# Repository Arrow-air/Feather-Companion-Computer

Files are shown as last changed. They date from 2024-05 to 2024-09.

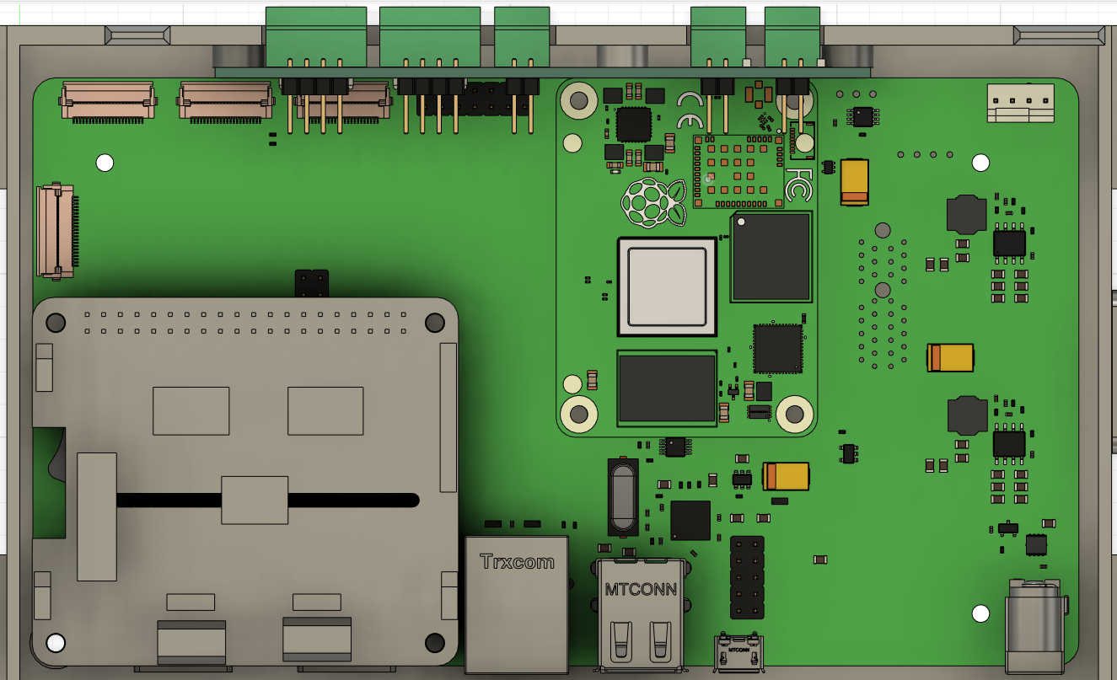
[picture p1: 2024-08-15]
Docs/FCPC Exposed Pic.png

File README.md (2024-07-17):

# Feather Flight Companion Computer

## Ground Control Station & Onboard Flight UI

### Functions:
1. Data Logger
2. Telemetry Server
3. User Interface Engine

## Table of Contents
1. [Introduction](#introduction)
2. [Architecture Overview](#architecture-overview)
3. [File Descriptions](#file-descriptions)
    - [FCPC.py](#fcpcpy)
    - [Data.py](#datapy)
    - [Veronte.py](#verontepy)
    - [BMS.py](#bmspy)
    - [VESCCAN.py](#vesccanpy)
    - [ESC.py](#escpy)
    - [CyphalCAN3.py](#cyphalcan3py)
    - [TCP.py](#tcppy)
    - [server.py](#serverpy)
    - [protocols_functions.py](#protocols_functionspy)
    - [display1.py](#display1py)
    - [display2.py](#display2py)
    - [Joystick.py](#joystickpy)
    - [LoRa.py](#lorapy)
    - [IO.py](#iopy)

## Introduction

The Flight Companion Computer system designed for both Ground Control Station (GCS) and onboard flight use (FUI). It integrates multiple functionalities including data logging, telemetry server, and a user interface engine. The system is modular, allowing for easy expansion and maintenance, and is designed to provide a robust Data interface for flight operations.

## Architecture Overview

The system is structured into multiple modules, each handling a specific aspect of the overall functionality. These modules include communication protocols, data handling, user interfaces, and specific hardware controls. The main control program loop resides in the `FCPC.py` file.

## File Descriptions

### FCPC.py
**Main Function and Control Logic**  
The central script that coordinates the activities of all other modules. Handles high-level decision making and ensures smooth operation of the entire system.

### Data.py
**Data Handling Module**  
Manages data storage and retrieval within the system. Provides functions for logging data, managing data formats, packaging data to be sent as telemetry.

### Veronte.py
**Veronte Module**  
Interfaces with the main Flight Controller, the Embention Veronte X1, over UART serial. packages flight sensor data, such as attitude and altitude etc.

### BMS.py
**Battery Management System (BMS) Module**  
Packages data from each of the 6 Ennoid X-LITE-V4 BMSs on board the aircraft, including voltage, current, temperature, and state of charge, etc.

### VESCCAN.py
**VESC-CAN Module**  
Interfaces with the VESC CAN bus protocol for interacting with data emminating from the Ennoid X-LITE-V4 BMSs, as implemented by Ennoid.

### ESC.py
**Electronic Speed Controller (ESC) Module**  
Packages data from each of the 6 Mad Motors ECSs on board the aircraft, including voltage, current, temperature, and state of charge, etc.

### CyphalCAN3.py
**Cyphal-CAN Protocol Module**  
Interfaces with the Cyphal-CAN CAN bus protocol for interacting with data emminating from the MAD Motors ECS, as implemented by MAD Motors.

### TCP.py
**TCP/IP Communication Module**  
Implements communication over TCP/IP, handling socket connections, data transmission, and reception over local network, send telemetry data to the displays.

### server.py
**Server Module**  
Sets up a network connection to `display1.py` and `display2.py` to send telementry data to the display screens

### protocols_functions.py
**Protocols Utility Functions Module**  
Contains utility functions used by `server.py`, `display1.py`, and `display2.py`. Provides common functionalities such as message parsing, checksum calculation, and other specific operations.

### display1.py
**Display Module 1**  
Responsible for rendering the "System State Window", primarily displaying data from the Flight Controller.

### display2.py
**Display Module 2**  
Responsible for rendering the "System Infromation Window", primarily displaying data from all the ESCs and BMSs.

### Joystick.py
**Joystick Input Module**  
Handles input from but Logitec USB and Otto CAN joystick devices. Reads joystick movements and button presses, translating their commands to the control system.

### LoRa.py
**Long Range Radio Communication Module**  
Implements communication over the LoRa protocol for long-range, low-power wireless communication. Handles message encoding, decoding, and transmission.

### IO.py
**Input-Output Module**  
Manages I/O on the RPI GPIO pins.

---

This README provides a comprehensive overview of the Project Feather system and its components. For detailed usage and additional information, refer to the documentation within each module and the main `FCPC.py` script, as well as the following reference documents:

## FCPC Concept Document 

[FCPC Concept]( https://docs.google.com/document/d/15r7cTYvV1hOLt8er7vyQtWU0twEOfAIIOQ0pdE-wRtA/edit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 )

## Project Feather Data Network & Ground Equipment Document

[Data Network & Ground Equipment]( https://docs.google.com/document/d/11VlSYsE245VFLZsYB7TvqWuuJ1UnPRjPKnnLWUzqcEM/edit )

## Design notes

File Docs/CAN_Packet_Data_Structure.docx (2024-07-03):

# CAN Packet Data Structure

CAN Packet | Frame ID | Extended Frame | Length | Signal | Start Bit | Length | Byte Order | Signed | Scale | Offset | Minimum | Maximum | Unit
CAN_PACKET_BMS_TEMPS | 11018 | Yes | 8 | NoOfCells | 15 | 8 | Big Endian | No | 1 | 0 | 0 | 1
| | | | auxVoltagesIndividual1 | 23 | 16 | Big Endian | No | 0.01 | 0
| | | | auxVoltagesIndividual2 | 39 | 16 | Big Endian | No | 0.01 | 0
| | | | auxVoltagesIndividual3 | 55 | 16 | Big Endian | No | 0.01 | 0
CAN_PACKET_BMS_V_TOT | 9738 | Yes | 8 | packVoltage | 7 | 32 | Big Endian | Yes | 1 | 0 | -3.4e+38 | 3.4e+38 | V
| | | | chargerVoltage | 39 | 32 | Big Endian | Yes | 1 | 0 | 0 | 1 | V
CAN_PACKET_BMS_I | 9994 | Yes | 8 | packCurrent1 | 7 | 32 | Big Endian | Yes | 1 | 0 | 0 | 1 | A
| | | | packCurrent2 | 39 | 32 | Big Endian | Yes | 1 | 0 | 0 | 1 | A
CAN_PACKET_BMS_AH_WH | 10250 | Yes | 8 | Ah_Counter | 7 | 32 | Big Endian | Yes | 1 | 0 | 0 | 1 | Ah
| | | | Wh_Counter | 39 | 32 | Big Endian | Yes | 1 | 0 | 0 | 1 | Wh
CAN_PACKET_BMS_V_CELL | 10506 | Yes | 8 | cellPoint | 7 | 8 | Big Endian | No | 1 | 0 | 0 | 48
| | | | NoOfCells | 15 | 8 | Big Endian | No | 1 | 0 | 0 | 48
| | | | cellVoltage10 | 23 | 16 | Big Endian | No | 0.001 | 0 | 0 | 1 | V
| | | | cellVoltage11 | 39 | 16 | Big Endian | No | 0.001 | 0 | 0 | 1 | V
| | | | cellVoltage12 | 55 | 16 | Big Endian | No | 0.001 | 0 | 0 | 1 | V
CAN_PACKET_BMS_BAL | 10762 | Yes | 8 | NoOfCells | 0 | 8 | Little Endian | Yes | 1 | 0
| | | | bal_state | 8 | 56 | Little Endian | Yes | 1 | 0 | 0 | 1
CAN_PACKET_BMS_SOC_SOH_TEMP_STAT | 11530 | Yes | 8 | cellVoltageLow | 7 | 16 | Big Endian | No | 0.001 | 0 | 0 | 1 | V
| | | | cellVoltageHigh | 23 | 16 | Big Endian | No | 0.001 | 0 | 0 | 1 | V
| | | | SOC | 39 | 8 | Big Endian | No | 0.392156863 | 0 | 0 | 1 | %
| | | | SOH | 47 | 8 | Big Endian | No | 0.3922 | 0 | 0 | 100 | %
| | | | tBattHi | 55 | 8 | Big Endian | No | 1 | 0 | 0 | 1 | C
| | | | BitF | 63 | 8 | Big Endian | No | 1 | 0 | 0 | 1
CAN_PACKET_BMS_HUM | 11274 | Yes | 6 | CAN_PACKET_BMS_TEMP0 | 7 | 16 | Big Endian | No | 0.01 | 0 | 0 | 1 | C
| | | | CAN_PACKET_BMS_HUM_HUM | 23 | 16 | Big Endian | No | 0.01 | 0 | 0 | 1 | %
| | | | CAN_PACKET_BMS_HUM_TEMP1 | 39 | 16 | Big Endian | No | 0.01 | 0 | 0 | 1 | C

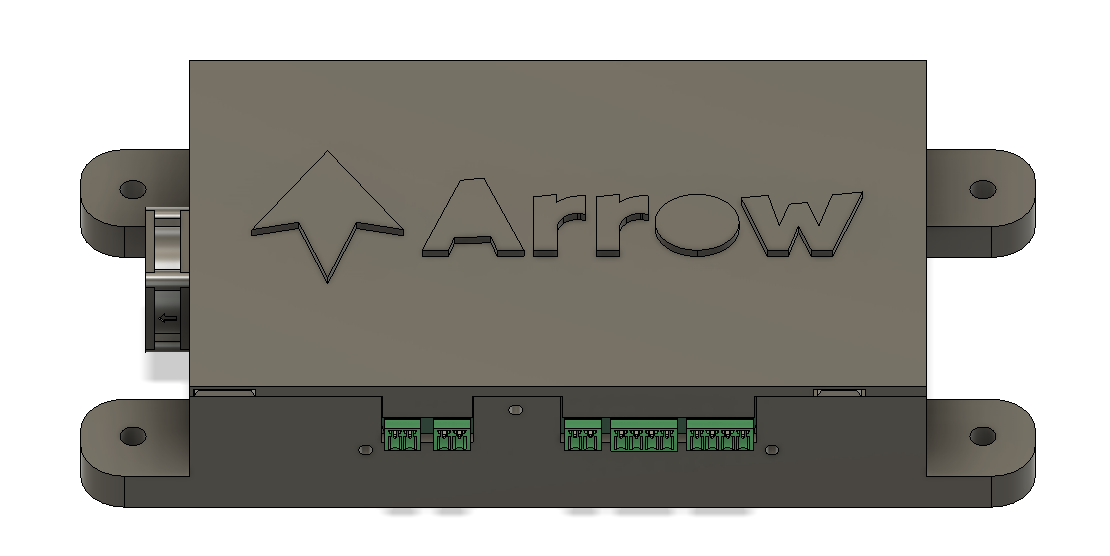
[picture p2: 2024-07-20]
Hardware/Enclosure/Front.png

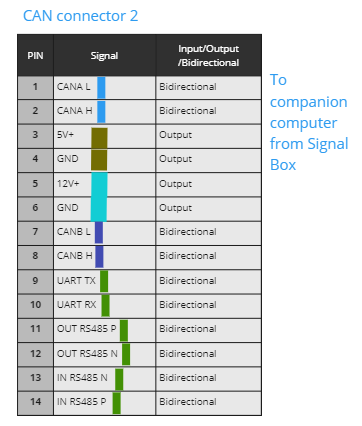
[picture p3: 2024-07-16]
Hardware/PCBs/FCPC Breakout PCB/Connectors to FCPC.PNG

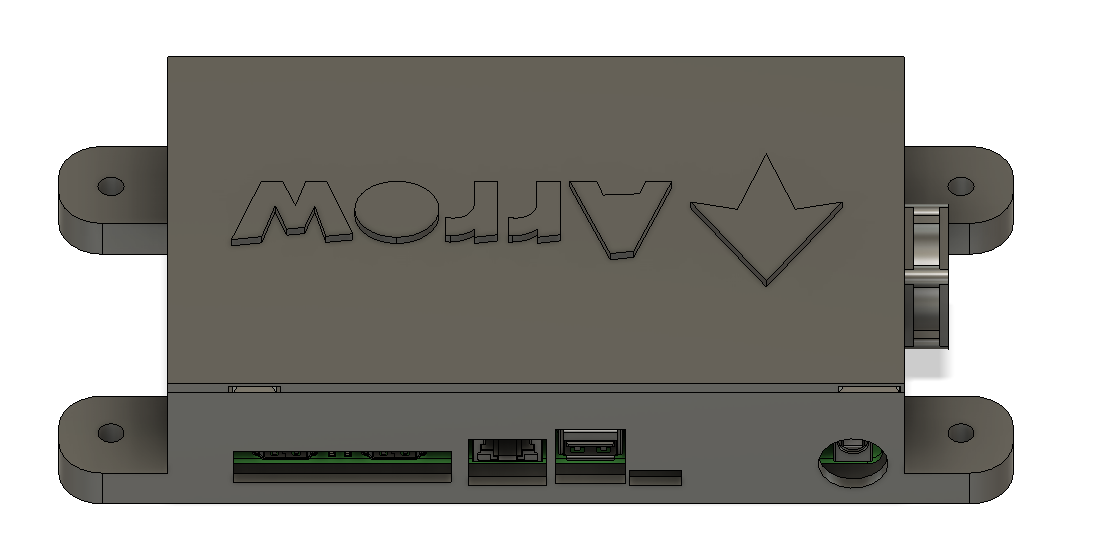
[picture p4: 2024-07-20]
Hardware/Enclosure/Back.png

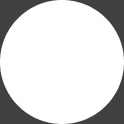
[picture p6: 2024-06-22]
images/inner circle.png

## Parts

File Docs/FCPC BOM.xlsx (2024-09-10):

Name | Description | Link | Price | Qty | Shipping + Tax | Total | Status | Notes
Companion PC | Raspberry Pi CM4 (NO WIFI NO Bluetooth) + IO Board (One on Craft Another on Ground) | https://www.digikey.co.uk/en/products/detail/raspberry-pi/SC0687/13530926 | $80.00 | 2 |  | $160.00 |  | Estimated
Displays | Groud station replica | https://www.elecrow.com/elecrow-10-1-inch-display-ips-1280x800-acrylic-case-touch-screen-compatible.html | $80.00 | 4 |  | $320.00 |  | Estimated
Control Sticks | Otto sticks, (or potential alternative (e.g Megatron)) | https://www.otto-controls.com/products/joysticks/Joystick%20Bases%20and%20Grips/HJLG3-M%20Joystick%20with%20Grip | $400.00 | 3 |  | $1,200.00 |  | Estimated
Enclosures + Mounting | Display mounts, 3D printed enclosures, etc | https://github.com/Arrow-air/Feather-Companion-Computer/tree/main/Hardware/Enclosure | $200.00 | 2 |  | $400.00 |  | Estimated
Cooling Fan |  | https://www.amazon.com/Dedicated-Cooling-Designed-Raspberry-Adjustment/dp/B09328RJK2 , https://www.waveshare.com/fan-4010-pwm-12v.htm | $7.90 | 2 |  | $15.8
Breakout PCB | Inhouse Design, wiring breakout Board | https://github.com/Arrow-air/Feather-Companion-Computer/tree/main/Hardware/PCBs/FCPC%20Breakout%20PCB | $25.00 | 2 |  | $50 |  | Estimated
CAN Module | 2 Channel RPi CAN Hat | https://www.waveshare.com/2-ch-can-hat.htm | $21.00 | 1 |  | $21.00
LoRa Modules | Telemetry Over LoRa Comms (HF Version, TCXO) | https://www.waveshare.com/usb-to-lora.htm | $17.99 | 2 |  | $35.98
LoRa Antenna | Range Extension and Location Flexibility (868MHZ version) | https://www.waveshare.com/868-915m-magnet-mount-antenna.htm?sku=24412 | $2.99 | 2 |  | $5.98
Powered USB Hub | 12V Power In over Barrel Jack Connector | e.g https://amzn.eu/d/gOa1naj | $20.00 | 2 |  | $40.00 |  | Estimated
FPV Camera & Transmitter |  | https://amzn.eu/d/8iTdUrI | $230.00 | 1 |  | $230.00 |  | Estimated
FPV Monitor |  | https://amzn.eu/d/cirWO3p | $120.00 | 1 |  | $120.00 |  | Estimated
Long Range WLAN Bridge | Point to Point Wireless Bridge | https://a.co/d/ivutc1m ( potential alternative e.g https://amzn.eu/d/02wFvdkK ) | $90.00 | 1 |  | $90.00 |  | Estimated

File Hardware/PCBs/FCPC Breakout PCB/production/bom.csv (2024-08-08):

Designator | Footprint | Quantity | Value | LCSC Part #
C1, C2 | 0805 | 2 | C
J1 | PhoenixContact_MCV_1,5_4-G-3.5_1x04_P3.50mm_Vertical | 1 | CAN
J10 | PinHeader_1x04_P2.54mm_Vertical | 1 | RS485
J2 | PhoenixContact_MCV_1,5_4-G-3.5_1x04_P3.50mm_Vertical | 1 | RS485
J3 | PhoenixContact_MCV_1,5_2-G-3.5_1x02_P3.50mm_Vertical | 1 | UART
J4 | PhoenixContact_MCV_1,5_2-G-3.5_1x02_P3.50mm_Vertical | 1 | 5V
J5 | PhoenixContact_MCV_1,5_2-G-3.5_1x02_P3.50mm_Vertical | 1 | 12V
J6 | PinHeader_1x02_P2.54mm_Vertical | 1 | UART
J7 | PinHeader_1x04_P2.54mm_Vertical | 1 | CAN
J8 | PinHeader_1x02_P2.54mm_Vertical | 1 | 5V
J9 | PinHeader_1x02_P2.54mm_Vertical | 1 | 12V
R1 | 0805 | 1 | 470
R2 | 0805 | 1 | 1K

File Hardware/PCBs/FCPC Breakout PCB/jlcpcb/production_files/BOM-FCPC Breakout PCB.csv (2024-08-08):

Comment | Designator | Footprint | LCSC
CAN | J1,J2 | PhoenixContact_MCV_1,5_4-G-3.5_1x04_P3.50mm_Vertical | C3580225
UART | J3,J4,J5 | PhoenixContact_MCV_1,5_2-G-3.5_1x02_P3.50mm_Vertical | C3582478
RS485 | J10 | PinHeader_1x04_P2.54mm_Vertical
12V | J9 | PinHeader_1x02_P2.54mm_Vertical
5V | J8 | PinHeader_1x02_P2.54mm_Vertical
CAN | J7 | PinHeader_1x04_P2.54mm_Vertical
UART | J6 | PinHeader_1x02_P2.54mm_Vertical
C | C2 | C_0805_2012Metric_Pad1.18x1.45mm_HandSolder
C | C1 | C_0805_2012Metric_Pad1.18x1.45mm_HandSolder
470 | R1 | R_0805_2012Metric_Pad1.20x1.40mm_HandSolder
1K | R2 | R_0805_2012Metric_Pad1.20x1.40mm_HandSolder

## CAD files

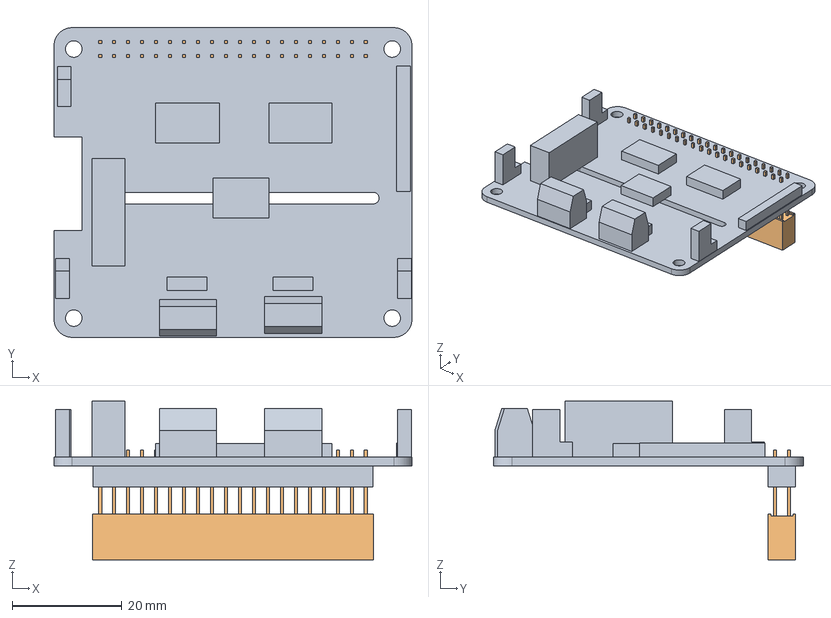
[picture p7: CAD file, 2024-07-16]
Hardware/PCBs/2-CH CAN HAT drawing/j25-2_asm.stp
65.2 x 56.4 x 28.9 mm
J25-2
J25-3

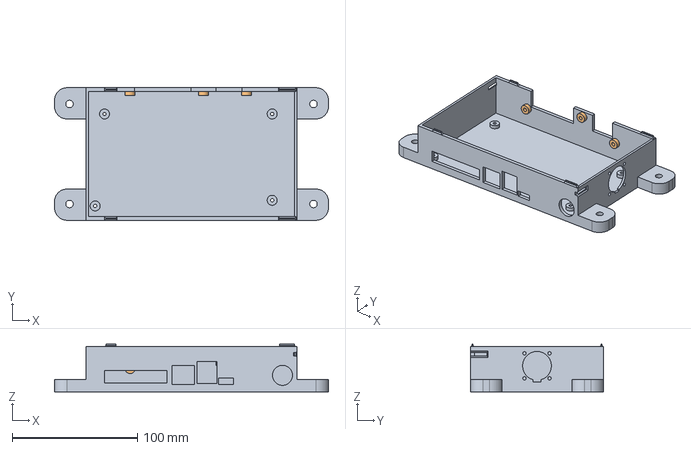
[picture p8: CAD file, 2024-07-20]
Hardware/Enclosure/Base.step
219.0 x 106.0 x 38.0 mm

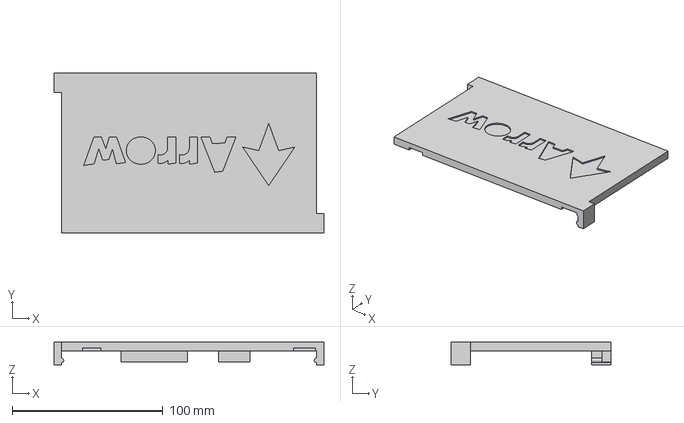
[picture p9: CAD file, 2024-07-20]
Hardware/Enclosure/Top.step
179.0 x 106.0 x 15.0 mm

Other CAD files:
Hardware/Enclosure/Top.stl

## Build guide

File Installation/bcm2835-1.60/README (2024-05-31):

This is a C library for Raspberry Pi (RPi). It provides access to 
GPIO and other IO functions on the Broadcom BCM 2835 chip.
allowing access to the 
26 pin ISE plug on the RPi board so you can control and interface with various
external devices.

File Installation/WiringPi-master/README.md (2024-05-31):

WiringPi (Unofficial Mirror/Fork)
=================================

This is an unofficial mirror/fork of wiringPi to support ports (Python/Ruby/etc).  With the
[end of official development](https://web.archive.org/web/20220405225008/http://wiringpi.com/wiringpi-deprecated/), this repository
has become a mirror of the last "official" source release, plus a fork facilitating updates
to support newer hardware (primarily for use by the ports) and fix bugs.

  * The final "official" source release can be found at the
    [`final_source_2.50`](https://github.com/WiringPi/WiringPi/tree/final_official_2.50) tag.
  * The default `master` branch contains code that has been written since that final source
    release to provide support for newer hardware.

Ports
-----

wiringPi has been wrapped for multiple languages:

* Node - https://github.com/WiringPi/WiringPi-Node
* Perl - https://github.com/WiringPi/WiringPi-Perl
* PHP - https://github.com/WiringPi/WiringPi-PHP
* Python - https://github.com/WiringPi/WiringPi-Python
* Ruby - https://github.com/WiringPi/WiringPi-Ruby

Support
-------

Please do not email Gordon if you have issues, he will not be able to help.

Pull-requests may be accepted to add or fix support for newer hardware, but new features or
other changes may not be accepted.

For support, comments, questions, etc please join the WiringPi Discord channel: https://discord.gg/SM4WUVG

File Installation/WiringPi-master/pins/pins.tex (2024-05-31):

\documentclass[12pt,a4paper]{article}
\parskip 1ex
\parindent 0em
\thispagestyle{empty}
\pagestyle{plain}
\pagenumbering{arabic}
\setlength{\topmargin}{0pt}
\setlength{\headheight}{0pt}
\setlength{\headsep}{0pt}
\setlength{\topskip}{0pt}
\setlength{\textheight}{240mm}
\setlength{\footskip}{5ex}
\setlength{\oddsidemargin}{0pt}
\setlength{\evensidemargin}{0pt}
\setlength{\textwidth}{160mm}
\usepackage[dvips]{graphics,color}
\usepackage{helvet}
\renewcommand{\familydefault}{\sfdefault}
\begin{document}
\begin{sffamily}
\definecolor{rtb-black}{rgb}  {0.0, 0.0, 0.0}
\definecolor{rtb-navy}{rgb}   {0.0, 0.0, 0.5}
\definecolor{rtb-green}{rgb}  {0.0, 0.5, 0.0}
\definecolor{rtb-teal}{rgb}   {0.0, 0.5, 0.5}
\definecolor{rtb-maroon}{rgb} {0.5, 0.0, 0.0}
\definecolor{rtb-purple}{rgb} {0.5, 0.0, 0.5}
\definecolor{rtb-olive}{rgb}  {0.5, 0.5, 0.0}
\definecolor{rtb-silver}{rgb} {0.7, 0.7, 0.7}
\definecolor{rtb-grey}{rgb}   {0.5, 0.5, 0.5}
\definecolor{rtb-blue}{rgb}   {0.0, 0.0, 1.0}
\definecolor{rtb-lime}{rgb}   {0.0, 1.0, 0.0}
\definecolor{rtb-aqua}{rgb}   {0.0, 1.0, 1.0}
\definecolor{rtb-red}{rgb}    {1.0, 0.0, 0.0}
\definecolor{rtb-fuchsia}{rgb}{1.0, 0.0, 1.0}
\definecolor{rtb-yellow}{rgb} {1.0, 1.0, 0.0}
\definecolor{rtb-white}{rgb}  {1.0, 1.0, 1.0}

\begin{center}
\bfseries{WiringPi: GPIO Pin Numbering Tables}\\
\tt{https://github.com/WiringPi/WiringPi}
\end{center}

\begin{center}
\begin{tabular}{|c|c|c||p{8mm}|p{8mm}||c|c|c|c|}
\hline
\multicolumn{8}{|c|}{\bfseries{P1: The Main GPIO connector}}\\
\hline
\hline
WiringPi Pin	& BCM GPIO	& Name	& \multicolumn{2}{|c||}{Header}	& Name	& BCM GPIO	& WiringPi Pin\\
\hline
\hline
	& 			& \textcolor{rtb-red}{3.3v}	& \raggedleft{1} &  2 & \textcolor{rtb-maroon}{5v}	& 	& \\
\hline
8	& Rv1:0 - Rv2:2		& \textcolor{rtb-aqua}{SDA}	& \raggedleft{3} &  4 & \textcolor{rtb-maroon}{5v}	& 	& \\
\hline
9	& Rv1:1 - Rv2:3		& \textcolor{rtb-aqua}{SCL}	& \raggedleft{5} &  6 & \textcolor{rtb-black}{0v}	& 	& \\
\hline
7	& 4			& \textcolor{rtb-green}{GPIO7}	& \raggedleft{7} &  8 & \textcolor{rtb-yellow}{TxD}	& 14    & 15\\
\hline
	& 			& \textcolor{rtb-black}{0v}	& \raggedleft{9} & 10 & \textcolor{rtb-yellow}{RxD}	& 15	& 16\\
\hline
0	& 17			& \textcolor{rtb-green}{GPIO0}	& \raggedleft{11} & 12 & \textcolor{rtb-green}{GPIO1}	& 18	& 1\\
\hline
2	& Rv1:21 - Rv2:27	& \textcolor{rtb-green}{GPIO2}	& \raggedleft{13} & 14 & \textcolor{rtb-black}{0v}	& 	& \\
\hline
3	& 22			& \textcolor{rtb-green}{GPIO3}	& \raggedleft{15} & 16 & \textcolor{rtb-green}{GPIO4}	& 23	& 4\\
\hline
	& 			& \textcolor{rtb-red}{3.3v}	& \raggedleft{17} & 18 & \textcolor{rtb-green}{GPIO5}	& 24	& 5\\
\hline
12	& 10			& \textcolor{rtb-teal}{MOSI}	& \raggedleft{19} & 20 & \textcolor{rtb-black}{0v}	& 	& \\
\hline
13	& 9			& \textcolor{rtb-teal}{MISO}	& \raggedleft{21} & 22 & \textcolor{rtb-green}{GPIO6}	& 25	& 6\\
\hline
14	& 11			& \textcolor{rtb-teal}{SCLK}	& \raggedleft{23} & 24 & \textcolor{rtb-teal}{CE0}	& 8	& 10\\
\hline
	& 			& \textcolor{rtb-black}{0v}	& \raggedleft{25} & 26 & \textcolor{rtb-teal}{CE1}	& 7	& 11\\
\hline
\hline
WiringPi Pin	& BCM GPIO	& Name	& \multicolumn{2}{|c||}{Header}	& Name	& BCM GPIO	& WiringPi Pin\\
\hline
\end{tabular}
\end{center}

Note the differences between Revision 1 and Revision 2 Raspberry
Pi's. The Revision 2 is readily identifiable by the presence of the 2
mounting holes.

The revision 2 Raspberry Pi has an additional GPIO connector, P5, which is next to the main P1 GPIO
connector:

\begin{center}
\begin{tabular}{|c|c|c||p{8mm}|p{8mm}||c|c|c|c|}
\hline
\multicolumn{8}{|c|}{\bfseries{P5: Secondary GPIO connector (Rev. 2 Pi only)}}\\
\hline
\hline
WiringPi Pin	& BCM GPIO	& Name	& \multicolumn{2}{|c||}{Header}	& Name	& BCM GPIO	& WiringPi Pin\\
\hline
\hline
	& 		& \textcolor{rtb-maroon}{5v}	& \raggedleft{1} &  2 & \textcolor{rtb-red}{3.3v}	& 	&	\\
\hline
17	& 28		& \textcolor{rtb-green}{GPIO8}	& \raggedleft{3} &  4 & \textcolor{rtb-green}{GPIO9}	& 29	& 18	\\
\hline
19	& 30		& \textcolor{rtb-green}{GPIO10}	& \raggedleft{5} &  6 & \textcolor{rtb-green}{GPIO11}	& 31	& 20	\\
\hline
	& 		& \textcolor{rtb-black}{0v}	& \raggedleft{7} &  8 & \textcolor{rtb-black}{0v}	& 	&	\\
\hline
\hline
WiringPi Pin	& BCM GPIO	& Name	& \multicolumn{2}{|c||}{Header}	& Name	& BCM GPIO	& WiringPi Pin\\
\hline
\end{tabular}
\end{center}

\end{sffamily}
\end{document}

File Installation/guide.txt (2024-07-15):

Fisrt make all shell scripts executable:
chmod +x enable_uart_spi.sh install_dependencies.sh configure_can.sh run_project.sh setup_and_run.sh

Run the master script:
sudo bash setup_and_run.sh

After the system reboots, manually run the following commands:
sudo bash install_dependencies.sh
sudo bash configure_can.sh
bash run_project.sh

replace "cd /path/to/your/project" with your actually python project path

**Run FUI FCPC.py First, then Run GCS FCPC.py

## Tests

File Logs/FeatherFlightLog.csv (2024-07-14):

{'altitude_AGL': 68.74 | 'altitude_AGL_set': 88.59 | 'altitude_ABS': 7.4 | 'heading': 9.69 | 'compass': 46.16 | 'attitude_pitch': 74.13 | 'attitude_roll': 42.67 | 'vertical_speed_KTS': 44.1 | 'airspeed_KTS': 74.59 | 'OAT': 62.94 | 'latitude': '40d26a46q' | 'longitude': '79d58a56q' | 'flight_time': '3:58' | 'command_pitch': '0.0' | 'command_roll': '0.0' | 'command_yaw': '0.0' | 'command_throttle': '-0.0' | 'switch_states': '024000' | 'parachute_state': 0 | 'BAT1_temp_C': 25 | 'BAT2_temp_C': 25 | 'BAT3_temp_C': 25 | 'BAT4_temp_C': 25 | 'BAT5_temp_C': 25 | 'BAT6_temp_C': 25 | 'ESC1_temp_C': 0 | 'ESC2_temp_C': 0 | 'ESC3_temp_C': 0 | 'ESC4_temp_C': 0 | 'ESC5_temp_C': 0 | 'ESC6_temp_C': 0 | 'MOT1_temp_C': 0 | 'MOT2_temp_C': 0 | 'MOT3_temp_C': 0 | 'MOT4_temp_C': 0 | 'MOT5_temp_C': 0 | 'MOT6_temp_C': 0 | 'BAT1_soc_PCT': 79 | 'BAT2_soc_PCT': 79 | 'BAT3_soc_PCT': 79 | 'BAT4_soc_PCT': 79 | 'BAT5_soc_PCT': 79 | 'BAT6_soc_PCT': 79 | 'MOT1_rpm_PCT': 0 | 'MOT2_rpm_PCT': 0 | 'MOT3_rpm_PCT': 0 | 'MOT4_rpm_PCT': 0 | 'MOT5_rpm_PCT': 0 | 'MOT6_rpm_PCT': 0 | 'ESC1_V': 0 | 'ESC2_V': 0 | 'ESC3_V': 0 | 'ESC4_V': 0 | 'ESC5_V': 0 | 'ESC6_V': 0 | 'ESC1_CUR_AMP': 0 | 'ESC2_CUR_AMP': 0 | 'ESC3_CUR_AMP': 0 | 'ESC4_CUR_AMP': 0 | 'ESC5_CUR_AMP': 0
{'altitude_AGL': 22.97 | 'altitude_AGL_set': 99.15 | 'altitude_ABS': 93.23 | 'heading': 72.34 | 'compass': 62.52 | 'attitude_pitch': 25.21 | 'attitude_roll': 75.39 | 'vertical_speed_KTS': 9.71 | 'airspeed_KTS': 42.03 | 'OAT': 5.97 | 'latitude': '40d26a46q' | 'longitude': '79d58a56q' | 'flight_time': '3:8' | 'command_pitch': '0.0' | 'command_roll': '0.0' | 'command_yaw': '0.0' | 'command_throttle': '-0.0' | 'switch_states': '024000' | 'parachute_state': 0 | 'BAT1_temp_C': 76 | 'BAT2_temp_C': 32 | 'BAT3_temp_C': 5 | 'BAT4_temp_C': 11 | 'BAT5_temp_C': 75 | 'BAT6_temp_C': 87 | 'ESC1_temp_C': 23 | 'ESC2_temp_C': 8 | 'ESC3_temp_C': 15 | 'ESC4_temp_C': 9 | 'ESC5_temp_C': 37 | 'ESC6_temp_C': 53 | 'MOT1_temp_C': 20 | 'MOT2_temp_C': 29 | 'MOT3_temp_C': 11 | 'MOT4_temp_C': 50 | 'MOT5_temp_C': 9 | 'MOT6_temp_C': 50 | 'BAT1_soc_PCT': 47 | 'BAT2_soc_PCT': 100 | 'BAT3_soc_PCT': 48 | 'BAT4_soc_PCT': 22 | 'BAT5_soc_PCT': 0 | 'BAT6_soc_PCT': 92 | 'MOT1_rpm_PCT': 604 | 'MOT2_rpm_PCT': 5867 | 'MOT3_rpm_PCT': 6896 | 'MOT4_rpm_PCT': 3578 | 'MOT5_rpm_PCT': 7523 | 'MOT6_rpm_PCT': 8504 | 'ESC1_V': 4 | 'ESC2_V': 38 | 'ESC3_V': 25 | 'ESC4_V': 51 | 'ESC5_V': 3 | 'ESC6_V': 19 | 'ESC1_CUR_AMP': 76 | 'ESC2_CUR_AMP': 79 | 'ESC3_CUR_AMP': 156 | 'ESC4_CUR_AMP': 191 | 'ESC5_CUR_AMP': 150
{'altitude_AGL': 14.51 | 'altitude_AGL_set': 75.37 | 'altitude_ABS': 63.19 | 'heading': 11.34 | 'compass': 6.49 | 'attitude_pitch': 25.86 | 'attitude_roll': 61.55 | 'vertical_speed_KTS': 64.69 | 'airspeed_KTS': 71.43 | 'OAT': 81.4 | 'latitude': '40d26a46q' | 'longitude': '79d58a56q' | 'flight_time': '50:18' | 'command_pitch': '0.0' | 'command_roll': '0.0' | 'command_yaw': '0.0' | 'command_throttle': '-0.0' | 'switch_states': '024000' | 'parachute_state': 0 | 'BAT1_temp_C': 25 | 'BAT2_temp_C': 25 | 'BAT3_temp_C': 25 | 'BAT4_temp_C': 25 | 'BAT5_temp_C': 25 | 'BAT6_temp_C': 25 | 'ESC1_temp_C': 45 | 'ESC2_temp_C': 29 | 'ESC3_temp_C': 12 | 'ESC4_temp_C': 2 | 'ESC5_temp_C': 21 | 'ESC6_temp_C': 13 | 'MOT1_temp_C': 52 | 'MOT2_temp_C': 41 | 'MOT3_temp_C': 22 | 'MOT4_temp_C': 46 | 'MOT5_temp_C': 49 | 'MOT6_temp_C': 14 | 'BAT1_soc_PCT': 79 | 'BAT2_soc_PCT': 79 | 'BAT3_soc_PCT': 79 | 'BAT4_soc_PCT': 79 | 'BAT5_soc_PCT': 79 | 'BAT6_soc_PCT': 79 | 'MOT1_rpm_PCT': 3880 | 'MOT2_rpm_PCT': 2752 | 'MOT3_rpm_PCT': 5173 | 'MOT4_rpm_PCT': 2998 | 'MOT5_rpm_PCT': 4598 | 'MOT6_rpm_PCT': 7067 | 'ESC1_V': 81 | 'ESC2_V': 75 | 'ESC3_V': 68 | 'ESC4_V': 20 | 'ESC5_V': 51 | 'ESC6_V': 0 | 'ESC1_CUR_AMP': 165 | 'ESC2_CUR_AMP': 89 | 'ESC3_CUR_AMP': 170 | 'ESC4_CUR_AMP': 50 | 'ESC5_CUR_AMP': 117
{'altitude_AGL': 77.23 | 'altitude_AGL_set': 10.14 | 'altitude_ABS': 64.04 | 'heading': 10.62 | 'compass': 85.6 | 'attitude_pitch': 65.45 | 'attitude_roll': 53.77 | 'vertical_speed_KTS': 93.42 | 'airspeed_KTS': 54.24 | 'OAT': 25.55 | 'latitude': '40d26a46q' | 'longitude': '79d58a56q' | 'flight_time': '11:32' | 'command_pitch': '0.0' | 'command_roll': '0.0' | 'command_yaw': '0.0' | 'command_throttle': '-0.0' | 'switch_states': '024000' | 'parachute_state': 0 | 'BAT1_temp_C': 25 | 'BAT2_temp_C': 25 | 'BAT3_temp_C': 25 | 'BAT4_temp_C': 25 | 'BAT5_temp_C': 25 | 'BAT6_temp_C': 25 | 'ESC1_temp_C': 58 | 'ESC2_temp_C': 4 | 'ESC3_temp_C': 19 | 'ESC4_temp_C': 20 | 'ESC5_temp_C': 29 | 'ESC6_temp_C': 44 | 'MOT1_temp_C': 29 | 'MOT2_temp_C': 16 | 'MOT3_temp_C': 45 | 'MOT4_temp_C': 1 | 'MOT5_temp_C': 9 | 'MOT6_temp_C': 41 | 'BAT1_soc_PCT': 79 | 'BAT2_soc_PCT': 79 | 'BAT3_soc_PCT': 79 | 'BAT4_soc_PCT': 79 | 'BAT5_soc_PCT': 79 | 'BAT6_soc_PCT': 79 | 'MOT1_rpm_PCT': 7093 | 'MOT2_rpm_PCT': 8849 | 'MOT3_rpm_PCT': 11831 | 'MOT4_rpm_PCT': 12370 | 'MOT5_rpm_PCT': 1803 | 'MOT6_rpm_PCT': 10898 | 'ESC1_V': 25 | 'ESC2_V': 2 | 'ESC3_V': 89 | 'ESC4_V': 92 | 'ESC5_V': 81 | 'ESC6_V': 13 | 'ESC1_CUR_AMP': 98 | 'ESC2_CUR_AMP': 43 | 'ESC3_CUR_AMP': 122 | 'ESC4_CUR_AMP': 155 | 'ESC5_CUR_AMP': 2
{'altitude_AGL': 22.06 | 'altitude_AGL_set': 72.1 | 'altitude_ABS': 50.81 | 'heading': 6.42 | 'compass': 22.96 | 'attitude_pitch': 17.81 | 'attitude_roll': 11.47 | 'vertical_speed_KTS': 76.5 | 'airspeed_KTS': 3.31 | 'OAT': 94.16 | 'latitude': '40d26a46q' | 'longitude': '79d58a56q' | 'flight_time': '11:13' | 'command_pitch': '0.0' | 'command_roll': '0.0' | 'command_yaw': '0.0' | 'command_throttle': '-0.0' | 'switch_states': '024000' | 'parachute_state': 0 | 'BAT1_temp_C': 25 | 'BAT2_temp_C': 25 | 'BAT3_temp_C': 25 | 'BAT4_temp_C': 25 | 'BAT5_temp_C': 25 | 'BAT6_temp_C': 25 | 'ESC1_temp_C': 40 | 'ESC2_temp_C': 49 | 'ESC3_temp_C': 38 | 'ESC4_temp_C': 58 | 'ESC5_temp_C': 15 | 'ESC6_temp_C': 46 | 'MOT1_temp_C': 20 | 'MOT2_temp_C': 59 | 'MOT3_temp_C': 12 | 'MOT4_temp_C': 26 | 'MOT5_temp_C': 39 | 'MOT6_temp_C': 7 | 'BAT1_soc_PCT': 79 | 'BAT2_soc_PCT': 79 | 'BAT3_soc_PCT': 79 | 'BAT4_soc_PCT': 79 | 'BAT5_soc_PCT': 79 | 'BAT6_soc_PCT': 79 | 'MOT1_rpm_PCT': 2888 | 'MOT2_rpm_PCT': 8270 | 'MOT3_rpm_PCT': 83 | 'MOT4_rpm_PCT': 4820 | 'MOT5_rpm_PCT': 12193 | 'MOT6_rpm_PCT': 8877 | 'ESC1_V': 13 | 'ESC2_V': 62 | 'ESC3_V': 29 | 'ESC4_V': 66 | 'ESC5_V': 72 | 'ESC6_V': 3 | 'ESC1_CUR_AMP': 10 | 'ESC2_CUR_AMP': 184 | 'ESC3_CUR_AMP': 97 | 'ESC4_CUR_AMP': 2 | 'ESC5_CUR_AMP': 36
{'altitude_AGL': 95.42 | 'altitude_AGL_set': 33.27 | 'altitude_ABS': 79.08 | 'heading': 72.34 | 'compass': 49.32 | 'attitude_pitch': 72.57 | 'attitude_roll': 55.36 | 'vertical_speed_KTS': 70.74 | 'airspeed_KTS': 69.95 | 'OAT': 23.02 | 'latitude': '40d26a46q' | 'longitude': '79d58a56q' | 'flight_time': '59:31' | 'command_pitch': '0.0' | 'command_roll': '0.0' | 'command_yaw': '0.0' | 'command_throttle': '-0.0' | 'switch_states': '024000' | 'parachute_state': 0 | 'BAT1_temp_C': 25 | 'BAT2_temp_C': 25 | 'BAT3_temp_C': 25 | 'BAT4_temp_C': 25 | 'BAT5_temp_C': 25 | 'BAT6_temp_C': 25 | 'ESC1_temp_C': 1 | 'ESC2_temp_C': 42 | 'ESC3_temp_C': 51 | 'ESC4_temp_C': 43 | 'ESC5_temp_C': 36 | 'ESC6_temp_C': 44 | 'MOT1_temp_C': 48 | 'MOT2_temp_C': 10 | 'MOT3_temp_C': 9 | 'MOT4_temp_C': 4 | 'MOT5_temp_C': 57 | 'MOT6_temp_C': 23 | 'BAT1_soc_PCT': 79 | 'BAT2_soc_PCT': 79 | 'BAT3_soc_PCT': 79 | 'BAT4_soc_PCT': 79 | 'BAT5_soc_PCT': 79 | 'BAT6_soc_PCT': 79 | 'MOT1_rpm_PCT': 5723 | 'MOT2_rpm_PCT': 2031 | 'MOT3_rpm_PCT': 12156 | 'MOT4_rpm_PCT': 4009 | 'MOT5_rpm_PCT': 5471 | 'MOT6_rpm_PCT': 3084 | 'ESC1_V': 47 | 'ESC2_V': 47 | 'ESC3_V': 55 | 'ESC4_V': 92 | 'ESC5_V': 68 | 'ESC6_V': 47 | 'ESC1_CUR_AMP': 134 | 'ESC2_CUR_AMP': 104 | 'ESC3_CUR_AMP': 18 | 'ESC4_CUR_AMP': 37 | 'ESC5_CUR_AMP': 65
{'altitude_AGL': 0.54 | 'altitude_AGL_set': 17.41 | 'altitude_ABS': 93.75 | 'heading': 16.41 | 'compass': 15.36 | 'attitude_pitch': 71.61 | 'attitude_roll': 34.61 | 'vertical_speed_KTS': 57.16 | 'airspeed_KTS': 95.4 | 'OAT': 14.84 | 'latitude': '40d26a46q' | 'longitude': '79d58a56q' | 'flight_time': '37:41' | 'command_pitch': '0.0' | 'command_roll': '0.0' | 'command_yaw': '0.0' | 'command_throttle': '-0.0' | 'switch_states': '024000' | 'parachute_state': 0 | 'BAT1_temp_C': 25 | 'BAT2_temp_C': 25 | 'BAT3_temp_C': 25 | 'BAT4_temp_C': 25 | 'BAT5_temp_C': 25 | 'BAT6_temp_C': 25 | 'ESC1_temp_C': 1 | 'ESC2_temp_C': 42 | 'ESC3_temp_C': 51 | 'ESC4_temp_C': 43 | 'ESC5_temp_C': 36 | 'ESC6_temp_C': 44 | 'MOT1_temp_C': 48 | 'MOT2_temp_C': 10 | 'MOT3_temp_C': 9 | 'MOT4_temp_C': 4 | 'MOT5_temp_C': 57 | 'MOT6_temp_C': 23 | 'BAT1_soc_PCT': 79 | 'BAT2_soc_PCT': 79 | 'BAT3_soc_PCT': 79 | 'BAT4_soc_PCT': 79 | 'BAT5_soc_PCT': 79 | 'BAT6_soc_PCT': 79 | 'MOT1_rpm_PCT': 5723 | 'MOT2_rpm_PCT': 2031 | 'MOT3_rpm_PCT': 12156 | 'MOT4_rpm_PCT': 4009 | 'MOT5_rpm_PCT': 5471 | 'MOT6_rpm_PCT': 3084 | 'ESC1_V': 47 | 'ESC2_V': 47 | 'ESC3_V': 55 | 'ESC4_V': 92 | 'ESC5_V': 68 | 'ESC6_V': 47 | 'ESC1_CUR_AMP': 134 | 'ESC2_CUR_AMP': 104 | 'ESC3_CUR_AMP': 18 | 'ESC4_CUR_AMP': 37 | 'ESC5_CUR_AMP': 65
{'altitude_AGL': 81.1 | 'altitude_AGL_set': 62.57 | 'altitude_ABS': 84.43 | 'heading': 87.28 | 'compass': 94.08 | 'attitude_pitch': 71.6 | 'attitude_roll': 43.25 | 'vertical_speed_KTS': 19.68 | 'airspeed_KTS': 28.6 | 'OAT': 53.71 | 'latitude': '40d26a46q' | 'longitude': '79d58a56q' | 'flight_time': '31:6' | 'command_pitch': '0.0' | 'command_roll': '0.0' | 'command_yaw': '0.0' | 'command_throttle': '-0.0' | 'switch_states': '024000' | 'parachute_state': 0 | 'BAT1_temp_C': 25 | 'BAT2_temp_C': 25 | 'BAT3_temp_C': 25 | 'BAT4_temp_C': 25 | 'BAT5_temp_C': 25 | 'BAT6_temp_C': 25 | 'ESC1_temp_C': 44 | 'ESC2_temp_C': 2 | 'ESC3_temp_C': 30 | 'ESC4_temp_C': 17 | 'ESC5_temp_C': 40 | 'ESC6_temp_C': 53 | 'MOT1_temp_C': 48 | 'MOT2_temp_C': 54 | 'MOT3_temp_C': 18 | 'MOT4_temp_C': 37 | 'MOT5_temp_C': 34 | 'MOT6_temp_C': 9 | 'BAT1_soc_PCT': 79 | 'BAT2_soc_PCT': 79 | 'BAT3_soc_PCT': 79 | 'BAT4_soc_PCT': 79 | 'BAT5_soc_PCT': 79 | 'BAT6_soc_PCT': 79 | 'MOT1_rpm_PCT': 9417 | 'MOT2_rpm_PCT': 12749 | 'MOT3_rpm_PCT': 9232 | 'MOT4_rpm_PCT': 1670 | 'MOT5_rpm_PCT': 10403 | 'MOT6_rpm_PCT': 4748 | 'ESC1_V': 10 | 'ESC2_V': 79 | 'ESC3_V': 63 | 'ESC4_V': 31 | 'ESC5_V': 0 | 'ESC6_V': 16 | 'ESC1_CUR_AMP': 124 | 'ESC2_CUR_AMP': 94 | 'ESC3_CUR_AMP': 153 | 'ESC4_CUR_AMP': 90 | 'ESC5_CUR_AMP': 41
{'altitude_AGL': 95.99 | 'altitude_AGL_set': 51.84 | 'altitude_ABS': 44.46 | 'heading': 84.88 | 'compass': 74.85 | 'attitude_pitch': 28.71 | 'attitude_roll': 99.69 | 'vertical_speed_KTS': 7.24 | 'airspeed_KTS': 26.7 | 'OAT': 76.23 | 'latitude': '40d26a46q' | 'longitude': '79d58a56q' | 'flight_time': '27:32' | 'command_pitch': '0.0' | 'command_roll': '0.0' | 'command_yaw': '0.0' | 'command_throttle': '-0.0' | 'switch_states': '024000' | 'parachute_state': 0 | 'BAT1_temp_C': 25 | 'BAT2_temp_C': 25 | 'BAT3_temp_C': 25 | 'BAT4_temp_C': 25 | 'BAT5_temp_C': 25 | 'BAT6_temp_C': 25 | 'ESC1_temp_C': 35 | 'ESC2_temp_C': 1 | 'ESC3_temp_C': 30 | 'ESC4_temp_C': 17 | 'ESC5_temp_C': 40 | 'ESC6_temp_C': 53 | 'MOT1_temp_C': 19 | 'MOT2_temp_C': 38 | 'MOT3_temp_C': 18 | 'MOT4_temp_C': 37 | 'MOT5_temp_C': 34 | 'MOT6_temp_C': 9 | 'BAT1_soc_PCT': 79 | 'BAT2_soc_PCT': 79 | 'BAT3_soc_PCT': 79 | 'BAT4_soc_PCT': 79 | 'BAT5_soc_PCT': 79 | 'BAT6_soc_PCT': 79 | 'MOT1_rpm_PCT': 8440 | 'MOT2_rpm_PCT': 7413 | 'MOT3_rpm_PCT': 9232 | 'MOT4_rpm_PCT': 1670 | 'MOT5_rpm_PCT': 10403 | 'MOT6_rpm_PCT': 4748 | 'ESC1_V': 16 | 'ESC2_V': 81 | 'ESC3_V': 63 | 'ESC4_V': 31 | 'ESC5_V': 0 | 'ESC6_V': 16 | 'ESC1_CUR_AMP': 167 | 'ESC2_CUR_AMP': 14 | 'ESC3_CUR_AMP': 153 | 'ESC4_CUR_AMP': 90 | 'ESC5_CUR_AMP': 41
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

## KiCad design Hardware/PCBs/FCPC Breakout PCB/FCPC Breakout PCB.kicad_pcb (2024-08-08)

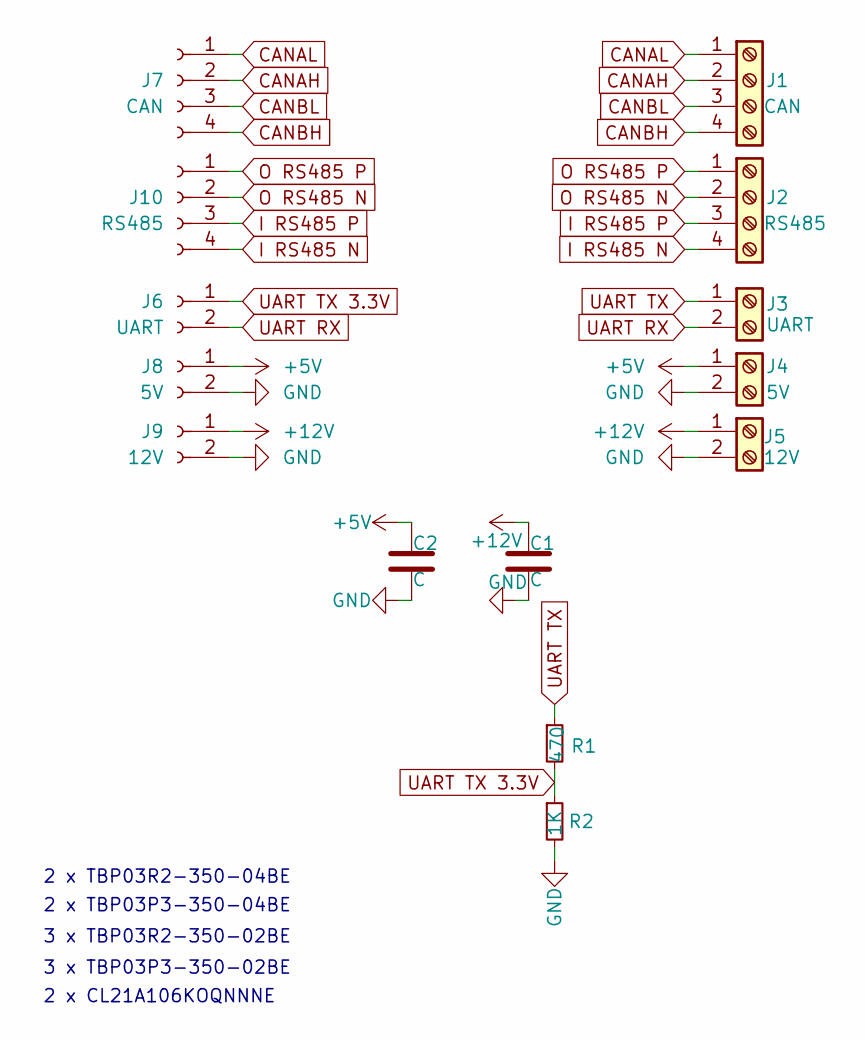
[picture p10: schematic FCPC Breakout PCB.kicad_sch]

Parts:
C1, C2: C; C_0805_2012Metric_Pad1.18x1.45mm_HandSolder
J1: CAN; PhoenixContact_MCV_1,5_4-G-3.5_1x04_P3.50mm_Vertical
J2: RS485; PhoenixContact_MCV_1,5_4-G-3.5_1x04_P3.50mm_Vertical
J3: UART; PhoenixContact_MCV_1,5_2-G-3.5_1x02_P3.50mm_Vertical
J4: 5V; PhoenixContact_MCV_1,5_2-G-3.5_1x02_P3.50mm_Vertical
J5: 12V; PhoenixContact_MCV_1,5_2-G-3.5_1x02_P3.50mm_Vertical
J6: UART; PinHeader_1x02_P2.54mm_Vertical
J7: CAN; PinHeader_1x04_P2.54mm_Vertical
J8: 5V; PinHeader_1x02_P2.54mm_Vertical
J9: 12V; PinHeader_1x02_P2.54mm_Vertical
J10: RS485; PinHeader_1x04_P2.54mm_Vertical
R1: 470; R_0805_2012Metric_Pad1.20x1.40mm_HandSolder
R2: 1K; R_0805_2012Metric_Pad1.20x1.40mm_HandSolder

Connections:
+5V: C2.1, J4.1, J8.1
+12V: C1.1, J5.1, J9.1
CANAH: J1.2, J7.2
CANAL: J1.1, J7.1
CANBH: J1.4, J7.4
CANBL: J1.3, J7.3
GND: C1.2, C2.2, J4.2, J5.2, J8.2, J9.2, R2.2
I RS485 N: J2.4, J10.4
I RS485 P: J2.3, J10.3
O RS485 N: J2.2, J10.2
O RS485 P: J2.1, J10.1
UART RX: J3.2, J6.2
UART TX: J3.1, R1.1
UART TX 3.3V: J6.1, R1.2, R2.1

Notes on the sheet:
2 x TBP03R2-350-04BE
2 x CL21A106KOQNNNE
3 x TBP03P3-350-02BE
2 x TBP03P3-350-04BE
3 x TBP03R2-350-02BE

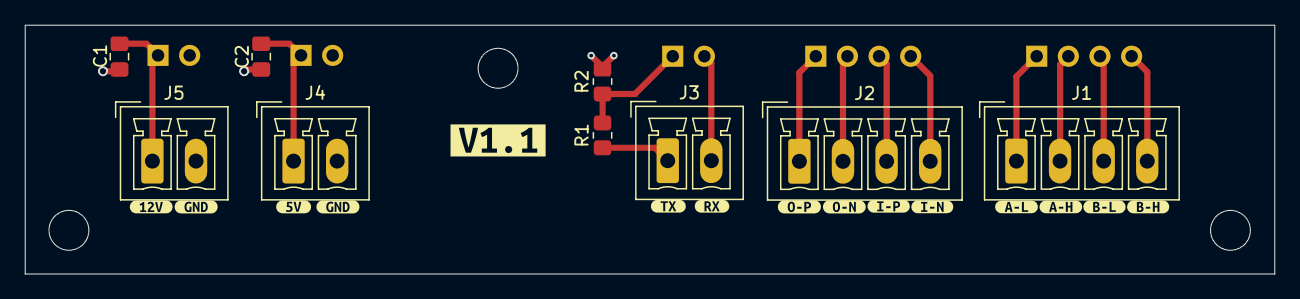
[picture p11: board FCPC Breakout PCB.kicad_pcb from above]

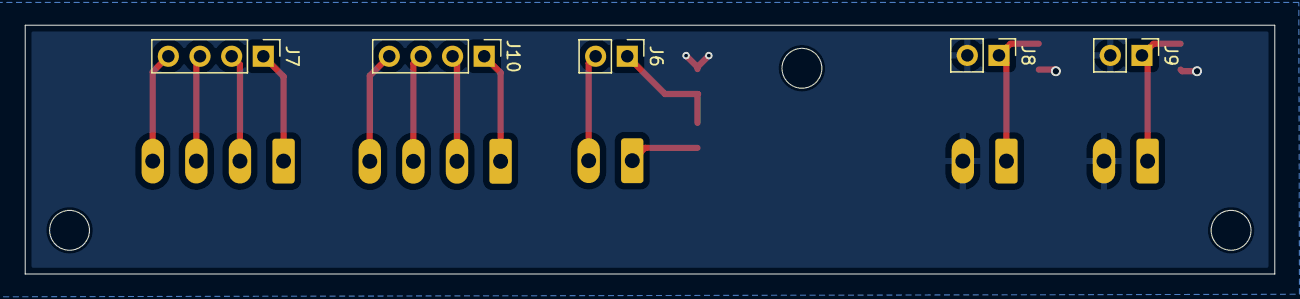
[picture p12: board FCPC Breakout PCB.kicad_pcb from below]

Board: 2 copper layers, 100.3 x 20.0 mm, 29 parts (5 on the bottom side), 14 nets.

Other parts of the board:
kibuzzard-66AD0A40: G***; kibuzzard-66AD0A40
kibuzzard-66AD0A64: G***; kibuzzard-66AD0A64
kibuzzard-6696DEDD, kibuzzard-6696DEDD#2: G***; kibuzzard-6696DEDD
kibuzzard-6696DEF0: G***; kibuzzard-6696DEF0
kibuzzard-6696DF0D: G***; kibuzzard-6696DF0D
kibuzzard-6696DF6D: G***; kibuzzard-6696DF6D
kibuzzard-6696DF63: G***; kibuzzard-6696DF63
kibuzzard-6696DFAD: G***; kibuzzard-6696DFAD
kibuzzard-6696DFC0: G***; kibuzzard-6696DFC0
kibuzzard-6696DFD9: G***; kibuzzard-6696DFD9
kibuzzard-6696E01E: G***; kibuzzard-6696E01E
kibuzzard-6696E02F: G***; kibuzzard-6696E02F
kibuzzard-6696E03F: G***; kibuzzard-6696E03F
kibuzzard-6696E054: G***; kibuzzard-6696E054

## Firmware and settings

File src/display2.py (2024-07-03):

import socket
import pygame, math
from pygame import gfxdraw
from protocols_functions import PROTOCOL_CLIENT, PROTOCOL_SERVER,DELIMITER, LENGTH_FIELD_LENGTH, extract_parameters_from_string

pygame.init()

SERVER_IP = "127.0.0.1"  # Our server will run on same computer as client
SERVER_PORT = 5680


class D2:
    def __init__(self,modeselect:str, display_num):
        self.mode = {0:'GCS',1:'FUI'}
        self.modeselect = modeselect

        try:
            self.server_socket = socket.socket(socket.AF_INET, socket.SOCK_STREAM) # create a socket,   socket.AF_INET = IP protocol,   socket.SOCK_STREAM = protocol TCP
            self.server_socket.connect((SERVER_IP,SERVER_PORT)) # connect to the socket(make it able to send messages in the socket)
        except:
            print("An error was raised\nThe server might be down or not started")

        if self.modeselect == self.mode.get(0):
            self.screen = pygame.display.set_mode((1860,1020), display=display_num)
            print(self.modeselect)
        elif self.modeselect == self.mode.get(1):
            self.screen = pygame.display.set_mode((1860,1020) ,display=display_num)
            print(self.modeselect)

        pygame.display.set_caption('UI Window D2')
        #pygame.display.set_icon(pygame.image.load('images/feather-icon.png'))

        self.small_font = pygame.font.SysFont('Corbel', int(self.screen.get_height()//40))
        self.medium_small_font = pygame.font.SysFont('Corbel', int(self.screen.get_height()//37.5))
        self.font = pygame.font.SysFont('Corbel', int(self.screen.get_height()//35))

        print('Display No: ' + str(pygame.display.get_num_displays()))
        print('Display Size: ' + str(pygame.display.get_window_size()))
        print('Screen size: ' + str(self.screen.get_size()))
        # both next 2 variable will be updated in the D2_func
        self.parameters = {
        }
        self.parameters_value_range = { # this is how much can the parameters move, if one has a range of -100 to 100 the value here will be 200
            
        }
        self.images = {
            "structure":pygame.image.load("images/structure.png"),
            "motor circle":pygame.image.load("images/circle image.png"),
        }
        self.images["structure"] = pygame.transform.smoothscale(self.images["structure"], ((self.images["structure"].get_width()/self.images["structure"].get_height())*self.screen.get_height()//2, self.screen.get_height()//2))
        self.images["motor circle"] = pygame.transform.smoothscale(self.images["motor circle"],(self.images["structure"].get_height()//2.1,self.images["structure"].get_height()//2.1))

        # setting up the motor images positions for faster running
        structure_size = self.images["structure"].get_size()
        structure_x = self.screen.get_width()//2 - structure_size[0]//2
        structure_y = self.screen.get_height()//2 - structure_size[1]//2
        self.motor_circle_size = self.images["motor circle"].get_size()
        self.motor_image_positions = [
            (structure_x - self.motor_circle_size[0]*0.8, structure_y - self.motor_circle_size[1]*0.8), # left top
            (structure_x - self.motor_circle_size[0]*1.1,structure_y + structure_size[1]//2 - self.motor_circle_size[1]//2), # left middle
            (structure_x - self.motor_circle_size[0]*0.8, structure_y  + structure_size[1] - self.motor_circle_size[1]//10), # left down
            (structure_x + structure_size[0] - self.motor_circle_size[0]*0.2, structure_y - self.motor_circle_size[1]*0.8), # right top
            (structure_x + structure_size[0] + self.motor_circle_size[0]*0.1, structure_y + structure_size[1]//2 - self.motor_circle_size[1]//2), # right middle
            (structure_x + structure_size[0] - self.motor_circle_size[0]*0.2, structure_y  + structure_size[1] - self.motor_circle_size[1]//10) # right down
        ]

        self.current_parameters_part = 1
        
    def draw_circle_info(self, motor_num,x,y,outer_circle_size, text_side):

        # BAT,ESC
        bat_value = self.parameters["BAT"+str(motor_num)+"_temp_C"]
        esc_value = self.parameters["ESC"+str(motor_num)+"_temp_C"]

        # drawing the battery color which is a ring around the motor circle
        battery_percentage = self.parameters["BAT"+str(motor_num)+"_soc_PCT"] / 100 # divide by 100 to get the percentage as a number between 0-1
        battery_ring_color = (255 - int(255*battery_percentage), int(255*battery_percentage),0)

        bat_esc_half_circle_pos = (x + self.images["motor circle"].get_width()//2,
                            y + self.images["motor circle"].get_height()//2)
        # BUT
        temp_to_max_ratio = bat_value/100
        if temp_to_max_ratio >= 1:
            temp_to_max_ratio = 1
        pygame.draw.circle(self.screen, (int(255*temp_to_max_ratio), 255 - int(255*temp_to_max_ratio),0),
                           bat_esc_half_circle_pos
                           ,outer_circle_size[0]//2, 0, draw_top_left=True,draw_bottom_left=True)
        # ESC
        temp_to_max_ratio = esc_value/100
        if temp_to_max_ratio >= 1:
            temp_to_max_ratio = 1
        pygame.draw.circle(self.screen, (int(255*temp_to_max_ratio), 255 - int(255*temp_to_max_ratio),0),
                           bat_esc_half_circle_pos
                           ,outer_circle_size[0]//2, 0, draw_top_right=True,draw_bottom_right=True)

        # drawing the border that indicates what is the battery
        circle_center = (x + outer_circle_size[0]//2, y + outer_circle_size[1]//2)
        for y2 in range(int(y - outer_circle_size[1]*0.2),int(y+outer_circle_size[1]*1.2)):
            for x2 in range(int(x - outer_circle_size[0]*0.2), int(x+outer_circle_size[0]*1.2)):
                distance_from_center = math.sqrt(math.pow(circle_center[0] - x2,2)+math.pow(circle_center[1] - y2,2))
                if distance_from_center >= outer_circle_size[0]//2 and distance_from_center <=  outer_circle_size[0]*(2.3/4):
                    d_y2_y = y2 - y
                    ratio_to_size = d_y2_y/outer_circle_size[1]
                    if ratio_to_size <= battery_percentage:
                        self.screen.set_at((x2,y2),battery_ring_color)

        # blitting the motor circle 
        self.screen.blit(self.images["motor circle"], (x,y))

        # rpm text
        self.screen.blit(self.small_font.render(str(self.parameters["MOT"+str(motor_num)+"_rpm_PCT"]),True,(0,0,0)), (x + outer_circle_size[0]//2 - self.small_font.size(str(self.parameters["MOT"+str(motor_num)+"_rpm_PCT"]))[0]//2,y + outer_circle_size[1]//2 - self.small_font.size("R")[1]))
        self.screen.blit(self.small_font.render("RPM",True,(100,100,100)), (x + outer_circle_size[0]//2 - self.small_font.size("RPM")[0]//2,y + outer_circle_size[1]//2))
        
        # BAT text
        BAT_text = str(bat_value) + "C"
        self.screen.blit(self.medium_small_font.render(BAT_text,True,(0,0,0)), (x + outer_circle_size[0]//2 - self.medium_small_font.size(BAT_text+"aa.")[0], y + outer_circle_size[1]//2+self.medium_small_font.size("A")[1]*1.1))
        self.screen.blit(self.medium_small_font.render("BAT",True,(0,0,0)), (x + outer_circle_size[0]//2 - self.medium_small_font.size("BAT"+"ab")[0], y + outer_circle_size[1]//2+self.medium_small_font.size("A")[1]*2.1))
        
        # ESC text
        ESC_text = str(esc_value) + "C"
        self.screen.blit(self.medium_small_font.render(ESC_text,True,(0,0,0)), (x + outer_circle_size[0]//2 + self.medium_small_font.size("aa.")[0], y + outer_circle_size[1]//2+self.medium_small_font.size("A")[1]*1.1))
        self.screen.blit(self.medium_small_font.render("ESC",True,(0,0,0)), (x + outer_circle_size[0]//2 + self.medium_small_font.size("ab")[0], y + outer_circle_size[1]//2+self.medium_small_font.size("A")[1]*2.1))

        # the text on the side
        if text_side =='l': # left side of the circle
            text_x = x - self.font.size("Volt: 12345")[0]
            self.screen.blit(self.font.render("Volt: "+str(self.parameters["ESC"+str(motor_num)+"_V"]),True,(255,255,255)), (text_x, y + outer_circle_size[1]//2 - self.font.size("V")[1]))
            self.screen.blit(self.font.render("Cur: "+str(self.parameters["ESC"+str(motor_num)+"_CUR_AMP"]),True,(255,255,255)), (text_x, y + outer_circle_size[1]//2))
            self.screen.blit(self.font.render("Power: "+str(self.parameters["ESC"+str(motor_num)+"_CUR_AMP"]*self.parameters["ESC"+str(motor_num)+"_V"]),True,(255,255,255)), (text_x, y + outer_circle_size[1]//2 + self.medium_small_font.size("P")[1]))
        else: # right side of the circle
            text_x = x + outer_circle_size[0] + self.font.size("45")[0]
            self.screen.blit(self.font.render("Volt: "+str(self.parameters["ESC"+str(motor_num)+"_V"]),True,(255,255,255)), (text_x, y + outer_circle_size[1]//2 - self.font.size("V")[1]))
            self.screen.blit(self.font.render("Cur: "+str(self.parameters["ESC"+str(motor_num)+"_CUR_AMP"]),True,(255,255,255)), (text_x, y + outer_circle_size[1]//2))
            self.screen.blit(self.font.render("Power: "+str(self.parameters["ESC"+str(motor_num)+"_CUR_AMP"]*self.parameters["ESC"+str(motor_num)+"_V"]),True,(255,255,255)), (text_x, y + outer_circle_size[1]//2 + self.medium_small_font.size("P")[1]))
        
    def draw(self):
        self.screen.fill((65, 95, 255))
        
        # structure
        structure_size = self.images["structure"].get_size()
        structure_x = self.screen.get_width()//2 - structure_size[0]//2
        structure_y = self.screen.get_height()//2 - structure_size[1]//2
        self.screen.blit(self.images["structure"], (structure_x,structure_y))

        # left top
        x,y = self.motor_image_positions[0]
        pygame.draw.line(self.screen, (255,255,255), (x+self.motor_circle_size[0]*0.85,y+self.motor_circle_size[1]*0.85), (x+self.motor_circle_size[0]*1.1,y+self.motor_circle_size[1]*1.1),10)
        self.draw_circle_info(1,x,y,self.motor_circle_size,'l')

        # left middle
        x,y = self.motor_image_positions[1]
        pygame.draw.line(self.screen, (255,255,255), (x+self.motor_circle_size[0]*0.9,y+self.motor_circle_size[1]//1.4), (x+self.motor_circle_size[0]*1.11,y+self.motor_circle_size[1]//1.4),10)
        self.draw_circle_info(3,x,y,self.motor_circle_size,'l')
        
        # left down
        x,y = self.motor_image_positions[2]
        pygame.draw.line(self.screen, (255,255,255), (x+self.motor_circle_size[0]*0.75,y + self.motor_circle_size[1]*0.1), (x+self.motor_circle_size[0]*0.9,y - self.motor_circle_size[1]*0.1),10)
        self.draw_circle_info(5,x,y,self.motor_circle_size,'l')

        # right top
        x,y = self.motor_image_positions[3]
        pygame.draw.line(self.screen, (255,255,255), (x+self.motor_circle_size[0]*0.15,y+self.motor_circle_size[1]*0.85), (x-self.motor_circle_size[0]*0.1,y+self.motor_circle_size[1]*1.1),10)
        self.draw_circle_info(2,x,y,self.motor_circle_size,'r')

        # right middle
        x,y = self.motor_image_positions[4]
        pygame.draw.line(self.screen, (255,255,255), (x+self.motor_circle_size[0]*0.1,y+self.motor_circle_size[1]//1.4), (x-self.motor_circle_size[0]*0.11,y+self.motor_circle_size[1]//1.4),10)
        self.draw_circle_info(4,x,y,self.motor_circle_size,'r')

        # right down
        x,y = self.motor_image_positions[5]
        pygame.draw.line(self.screen, (255,255,255), (x+self.motor_circle_size[0]*0.25,y + self.motor_circle_size[1]*0.1), (x+self.motor_circle_size[0]*0.1,y - self.motor_circle_size[1]*0.1),10)
        self.draw_circle_info(6,x,y,self.motor_circle_size,'r')
      
    def build_message(self,cmd, data):
        """
        Gets command name (str) and data field (str) and creates a valid protocol message
        Returns: str, or None if error occured
        example of the function:
        build_message("LOGIN", "aaaa#bbbb") will return "LOGIN           |0009|aaaa#bbbb"
        """
        """get the command plus data and return the protocol message(what parse_message gets)"""

        protocol_message = ""
        num = len(data)
        if len(str(num)) < LENGTH_FIELD_LENGTH: # create the message and the message length(009,0100)
            num1 = LENGTH_FIELD_LENGTH - len(str(num))
            num = "0"*num1 + str(num)
        protocol_message += str(cmd) + DELIMITER + num + DELIMITER + str(data) # implement everything you did in the function to the protocol that send   DELIMITER = |

        return protocol_message
    def build_and_send_message(self,conn, code, data): # code = command
        message = self.build_message(code,data) # create the message( will look like this: LOGIN           |0009|aaaa#bbbb)
        
        print("[CLIENT]:", message)
        
        conn.send(message.encode()) # send to the server the message in the right format
    def parse_message(self,data):
        """
        Parses protocol message and returns command name and data field
        Returns: cmd (str), data (str). If some error occured, returns None, None
        """
        "get the message(what build_message returns) and need to return the command and the data"
        split_data = data.split(DELIMITER)
        cmd,length,data = split_data
        return cmd,data
    def recv_message_and_parse(self,conn):
        full_msg = conn.recv(1024).decode() # gets the message from the server   need to be something like this for example "LOGIN           |0009|aaaa#bbbb"
        cmd, data = self.parse_message(full_msg) # split it to a tuple with the command and the data
        
        print("[SERVER]:", full_msg)
        return cmd, data
    
    def send_and_receive_message(self):
        self.build_and_send_message(self.server_socket, "MESSAGE", "test")

        command,data = self.recv_message_and_parse(self.server_socket)
    def receive_parameters(self):
        if self.current_parameters_part == 1:
            param_part = "1"
            self.current_parameters_part = 2
        else:
            param_part = "2"
            self.current_parameters_part = 1
        self.build_and_send_message(self.server_socket, PROTOCOL_CLIENT["ask parameters"], param_part)
        cmd,data = self.recv_message_and_parse(self.server_socket)
        if cmd == PROTOCOL_SERVER["give parameters"]:
            updated_params = extract_parameters_from_string(data)
            for key in updated_params:
                self.parameters[key] = updated_params[key]


def D2_func(parameters_dict, display_num):
    D2_ui = D2("FUI",display_num)
    # update the class parameters
    D2_ui.parameters = parameters_dict

    print("Connected to the server: [SERVER]"+str(SERVER_IP)+":"+str(SERVER_PORT))

    running = True
    while running:
        D2_ui.receive_parameters()
        D2_ui.draw()

        for event in pygame.event.get():
            if event.type == pygame.QUIT:
                pygame.quit()
                running = False


        pygame.display.update()

parameters = {
    "altitude_AGL":0,
    "altitude_AGL_set":0,
    "altitude_ABS":0,
    "heading":0,
    "compass":0,
    "attitude_pitch":0, # forward-backward rotation of the aircraft itself, in what angle the aircraft is leaning to forward or backward, range: -180 to 180(minus is leaning backward, positive is leaning forward)
    "attitude_roll":0, # right-left rotation of the aircraft itself, in what angle the aircraft is leaning side wise, range: -180 to 180(minus is leaning to the left side, positive is to the right side)
    "vertical_speed_KTS":0,
    "airspeed_KTS":0, # warning range: 55-60,-60-(-55), [kts], speed will be between 0-60 knots
    "OAT":0, # warning range: 30-max=100
    "latitude":"""40° 26' 46" N""",
    "longitude":"""79° 58' 56" W""",
    "flight_time":"38:15",
    "command_pitch":0, # right joystick, up-down, range: -1 to 1
    "command_roll":0, # right joystick, left-right, range: -1 to 1
    "command_throttle":0, # left joystick, up-down, range: -1 to 1
    "command_yaw":0, # left joystick, left-right, range: -1 to 1
    "switch_states":0,
    "parachute_state":0,

    "BAT1_temp_C":90, # warning range: 80-180
    "BAT2_temp_C":10, # warning range: 80-180
    "BAT3_temp_C":40, # warning range: 80-180
    "BAT4_temp_C":90, # warning range: 80-180
    "BAT5_temp_C":85, # warning range: 80-180
    "BAT6_temp_C":50, # warning range: 80-180

    "ESC1_temp_C":60,
    "ESC2_temp_C":70,
    "ESC3_temp_C":20,
    "ESC4_temp_C":40,
    "ESC5_temp_C":10,
    "ESC6_temp_C":30,

    "MOT1_temp_C":0,
    "MOT2_temp_C":0,
    "MOT3_temp_C":0,
    "MOT4_temp_C":0,
    "MOT5_temp_C":0,
    "MOT6_temp_C":0,

    "BAT1_soc_PCT":12, # the percentage of the battery left, warning range: 1-15
    "BAT2_soc_PCT":100, # the percentage of the battery left, warning range: 1-15
    "BAT3_soc_PCT":100, # the percentage of the battery left, warning range: 1-15
    "BAT4_soc_PCT":57, # the percentage of the battery left, warning range: 1-15
    "BAT5_soc_PCT":80, # the percentage of the battery left, warning range: 1-15
    "BAT6_soc_PCT":40, # the percentage of the battery left, warning range: 1-15

    "MOT1_rpm_PCT":130, # warning range: 120-max=140
    "MOT2_rpm_PCT":0, # warning range: 120-max=140
    "MOT3_rpm_PCT":0, # warning range: 120-max=140
    "MOT4_rpm_PCT":0, # warning range: 120-max=140
    "MOT5_rpm_PCT":0, # warning range: 120-max=140
    "MOT6_rpm_PCT":0, # warning range: 120-max=140

    "ESC1_V":0,
    "ESC2_V":0,
    "ESC3_V":0,
    "ESC4_V":0,
    "ESC5_V":0,
    "ESC6_V":0,
    
    "ESC1_CUR_AMP":0,
    "ESC2_CUR_AMP":0,
    "ESC3_CUR_AMP":0,
    "ESC4_CUR_AMP":0,
    "ESC5_CUR_AMP":0,
    "ESC6_CUR_AMP":0,
    "TimeStamp":0
}

if __name__ == '__main__':
    D2_func(parameters, 0)

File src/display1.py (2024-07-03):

import socket
import pygame
from pygame import gfxdraw
from protocols_functions import PROTOCOL_CLIENT, PROTOCOL_SERVER,DELIMITER, LENGTH_FIELD_LENGTH, extract_parameters_from_string

pygame.init()

SERVER_IP = "127.0.0.1"  # Our server will run on same computer as client
SERVER_PORT = 5680


class D1:
    def __init__(self,modeselect:str, display_num):
        self.mode = {0:'GCS',1:'FUI'}
        self.modeselect = modeselect

        try:
            self.server_socket = socket.socket(socket.AF_INET, socket.SOCK_STREAM) # create a socket,   socket.AF_INET = IP protocol,   socket.SOCK_STREAM = protocol TCP
            self.server_socket.connect((SERVER_IP,SERVER_PORT)) # connect to the socket(make it able to send messages in the socket)
        except:
            pass

        if self.modeselect == self.mode.get(0):
            self.screen = pygame.display.set_mode((1860,1020), display=display_num)
            print(self.modeselect)
        elif self.modeselect == self.mode.get(1):
            self.screen = pygame.display.set_mode((1860,1020) ,display=display_num)
            print(self.modeselect)

        pygame.display.set_caption('UI Window D1')
        #pygame.display.set_icon(pygame.image.load('images/feather-icon.png'))

        self.font = pygame.font.SysFont('Corbel', int(self.screen.get_height()//30))
        self.medium_font = pygame.font.SysFont('Corbel', int(self.screen.get_height()//25))
        self.bigger_font = pygame.font.SysFont('Corbel', int(self.screen.get_height()//15))

        print('Display No: ' + str(pygame.display.get_num_displays()))
        print('Display Size: ' + str(pygame.display.get_window_size()))
        print('Screen size: ' + str(self.screen.get_size()))
        # both next 2 variable will be updated in the D1_func
        self.parameters = {
        }
        self.parameters_value_range = { # this is how much can the parameters move, if one has a range of -100 to 100 the value here will be 200
            "airspeed_KTS":60
        }

        self.images = {
            "compass":pygame.transform.smoothscale(pygame.image.load("images/compass.png"),(self.screen.get_height()//3.5*1.2,self.screen.get_height()//3.5*1.2)),
            "roll":pygame.transform.smoothscale(pygame.image.load("images/roll image.png"),(self.screen.get_height()//3.5*1.2,self.screen.get_height()//3.5*1.2)),
            "pointer above roll":pygame.image.load("images/pointer above roll.png"),
            "pointer":pygame.image.load("images/pointer.png")
        }
        roll_pointer_ratio = self.images["pointer above roll"].get_height() / self.images["pointer above roll"].get_width()
        self.images["pointer above roll"] = pygame.transform.smoothscale(self.images["pointer above roll"], (self.screen.get_height()//3.5,self.screen.get_height()//3.5*roll_pointer_ratio))
        self.images["pointer"] = pygame.transform.smoothscale(self.images["pointer"], (self.images["compass"].get_width()//10,self.images["compass"].get_width()//10))
        
        self.current_parameters_part = 1
    def check_for_warning(self):
        warning_variables = []

        for key, value in self.parameters.items():
            if key.endswith('_KTS'):
                if abs(value) >= 55 and abs(value) <= 60:
                    warning_variables.append(key)
            elif key.endswith('_temp_C'):
                if value >= 80 and value <= 180:
                    warning_variables.append(key)
            elif key.endswith('_soc_PCT'):
                if value >= 1 and value <= 15:
                    warning_variables.append(key)
            elif key.endswith('_rpm_PCT'):
                if value >= 120 and value <= 140:
                    warning_variables.append(key)
            elif key == 'OAT':
                if value >= 30 and value <= 100:
                    warning_variables.append(key)

        return warning_variables

    def draw_transparent_rect(self,win,size,alpha_level,color,pos, border_width = None, border_radius=5):
        transparent_surface = pygame.Surface((size[0], size[1]), pygame.SRCALPHA)
        if border_width == None:
            pygame.draw.rect(transparent_surface,(color[0],color[1],color[2],alpha_level) , (0, 0, size[0], size[1]), border_radius=border_radius)
        else:
            pygame.draw.rect(transparent_surface,(color[0],color[1],color[2],alpha_level) , (0, 0, size[0], size[1]), border_width, border_radius=border_radius)
        win.blit(transparent_surface, (pos[0],pos[1]))

    def draw(self):
        self.screen.fill((65, 95, 255))

        # show the warnings
        # warning are on the Left screen(Left part of the window)(D1)
        warnings = self.check_for_warning()
        if warnings != []:
            #warnings = ", ".join(warnings)
            #text = "Warning: " + warnings + " has exceeded tolerance!"
            text = "Warning: " + ", ".join(warnings) + " has exceeded tolerance!"

            max_text_width = self.screen.get_width()//5*4
            x =  self.screen.get_width() - max_text_width - self.bigger_font.size("5")[0] # the warnings are on the right part of the first screen(D1), doing minus the size of 5 because there are the lines of the height and this is how they are made
            y = 20 # leaving space for the speed text

            current_text = ""
            text_lines = []
            # splitting the text into lines because it is too long for 1 line sometimes
            for word in text.split(" "):
                # if text is too long
                if self.font.size(current_text+" " + word)[0] > max_text_width:
                    text_lines.append(current_text)
                    current_text = word
                # if text is not too long
                else:
                    current_text += word + " "
                    if word == text.split(" ")[-1]:
                        text_lines.append(current_text)

            max_length_text = max(text_lines, key=len)
            if max_length_text[-1] == " ":
                max_length_text = max_length_text[:-1]
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

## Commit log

2024-07-24 Update FCPC BOM.xlsx
    [FCPC BOM.xlsx]
2024-08-02 FPCP Breakout PCB Update:
    B - L to B - H on error fix on silk screen
    V 1.1 Board created
    [FCPC Breakout PCB-CuBottom.gbr, FCPC Breakout PCB-CuTop.gbr, FCPC Breakout PCB-EdgeCuts.gbr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]
2024-08-05 single motor test
    CyphalCAN3 modified to read single motor data for test
    (RPM calculation added = 3 * ES)
2024-08-08 PCB Update
    UART Voltage Divider 5V -> 3.3V
    [BOM-FCPC Breakout PCB.csv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]
2024-08-17 Update
    Complete ESC & BMS Log dumpout to csv file
    ESC.py CAN ID update
    Test on CyphalCAN3 added
2024-08-18 Update
    Enclosure made taller for easier wiring
    [Top.stl]
2024-08-25 throttle read update
2024-09-01 update enclosure
2024-10-14 update to BMS variable count 28 vs 27
2024-10-15 esc read update
2024-10-15 update print
2024-10-15 update data return point esc.py cancyphal.3py
